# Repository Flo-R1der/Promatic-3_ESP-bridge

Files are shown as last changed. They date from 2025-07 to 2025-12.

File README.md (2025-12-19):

# HÖRMANN Promatic 3 ESPHome Bridge

This project is made to integrate the Hörmann Promatic 3 garage door drive unit into Home Assistant using ESPHome. This approach is more sophisticated compared to other solutions like using an Shelly or similar devices, but comes with some extra functionality:

- ✅ Detects `opening` and `closing` (motor running) as well as `open`/`close` (end position)
- ✅ Does support partially opened states, like `10%` for air ventilation (with auto-stop)
- ✅ can be linked with a Beacon device for zero-touch offline opening
- ✅ is detecting wrong directions and switching the direction if required to gain more specific control, beside the one-touch control
- ✅ highly customizable
- ⚠️ requires PCB assembly and soldering
- ⚠️ requires ESPHome to flash the ESP firmware

> [!CAUTION]  
> Read the [official Manual](TR10A147_E_ProMatic_3_DE.pdf) for safety instruction. Never work on 230V when your're not an expert. Unplug the device before start working for your own safety and to prevent damages while assembling.

| Qty. | Ref.  | Part | Notes |
| :--: | :---: | :--- | :---- |
| 1 | A1 | **MP1584** 3,3V buck regulator | provides 3,3V stabilized; Input: 4,5–28 V |
| 1 | A2 | **ESP8266** D1 Mini or **ESP32** C3 Mini | use ESP32 version for BLE Support |
| 4 | U1-U4 | **PC819** optocoupler | for 24V/3,3V separation |
| 2 | R1-R2 | **2,2kΩ ½W** resistor | series resistor optocoupler LED at 24V |
| 2 | R3-R4 | **330Ω ¼W** resistor | series resistor optocoupler LED at 3,3V |
| 2 | C1-C2 | **0,47μF 35V** capacitor | catch voltage peaks from the driving motor |
| 1 | B1 | **reed switch** | to retrieve the "open" position |
| 1 | S1 | **momentary switch** | optional; for manual open/close/stop trigger |
| 1 | J1 | 2 leg **screw terminal** |  |
| 1 | J2 | 4 leg **screw terminal** |  |
| 1 | J3 | 3 leg **screw terminal** |  |

 A housing is also recommended since the PCB does not fit in the Promatic 3 housing. As reference: I'm using these [project boxes](https://www.amazon.de/dp/B0BWLW941S).

## Option 1: ESP8266 D1 mini
<details>
<summary>For basic functionalities the ESP8266 is totally suitable</summary>

### Circuit Diagram
ESP8266 circuit diagram

### PCB-Design
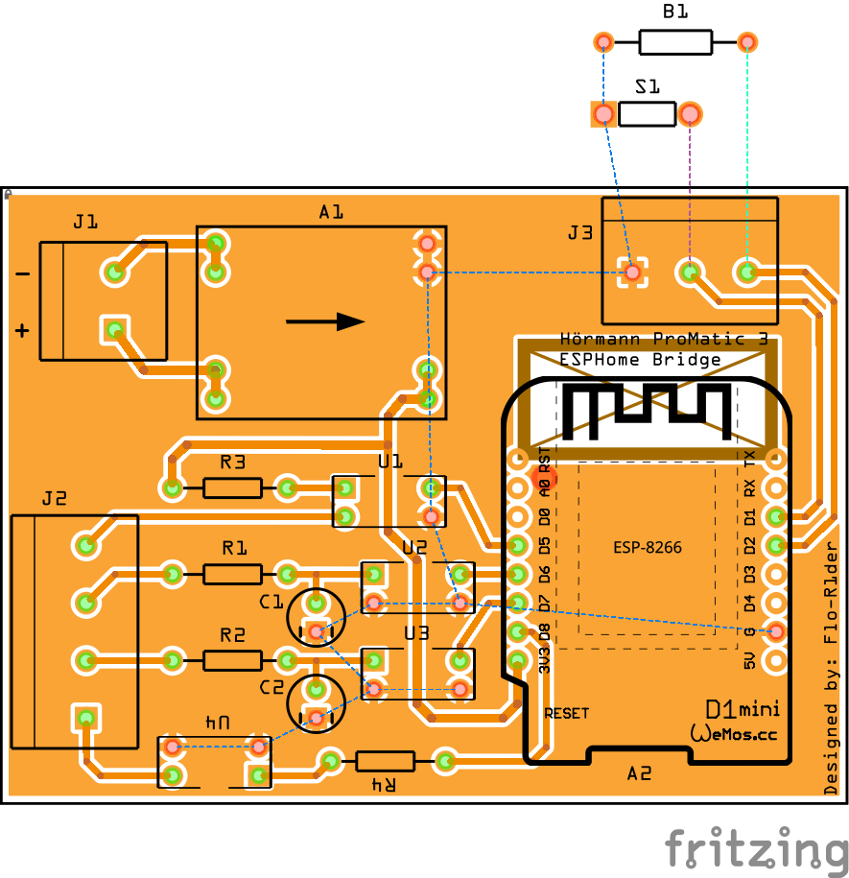
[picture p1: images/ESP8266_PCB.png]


If you like to order the PCB shown above, feel free to use the already exported production files. Or implement changes using **[fritzing](https://fritzing.org/download)** (check the [ESP8266 Pinout Reference](https://randomnerdtutorials.com/esp8266-pinout-reference-gpios/#wemos-d1-mini-pinout)!):
- **PCB-Design**: [ESP8266_extended-gerber.zip](ESP8266_extended-gerber.zip) (76 x 55,7mm)
- **Project File**: [ESP8266.fzz](ESP8266.fzz)

### Results (grid PCB)

I did my prototype on a grip PCB which also works great.  
Grid PCB: 70 x 50 mm / 24 x 18 holes / resistors vertical to save space

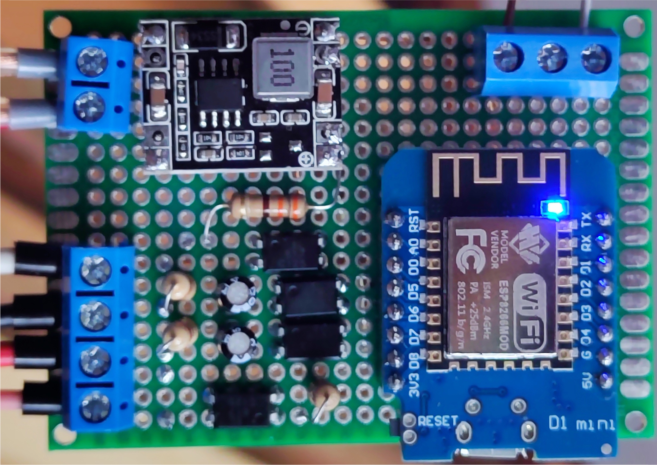
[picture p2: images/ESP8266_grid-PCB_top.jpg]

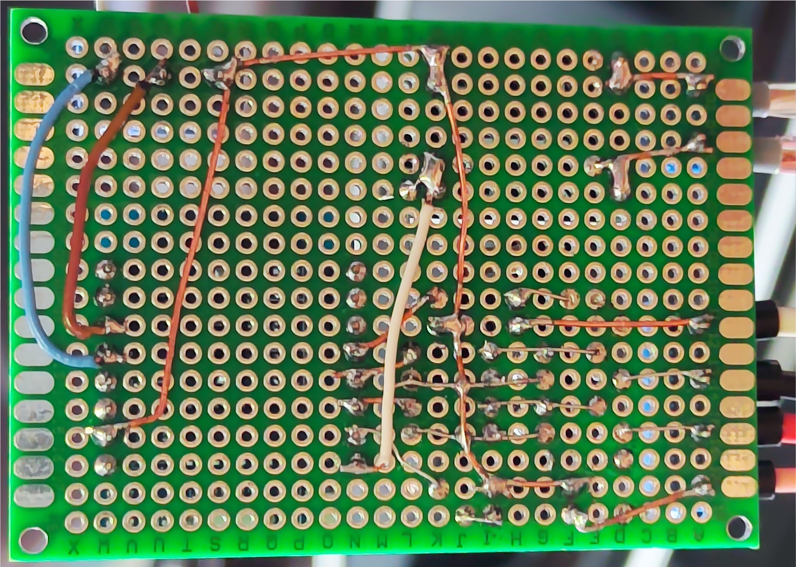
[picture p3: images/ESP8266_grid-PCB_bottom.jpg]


</details>

## Option 2: ESP32 C3 mini
<details>
<summary>For extended functionalities the ESP32 is the better option</summary>

### Circuit Diagram
ESP32-C3-mini circuit diagram

### PCB-Design
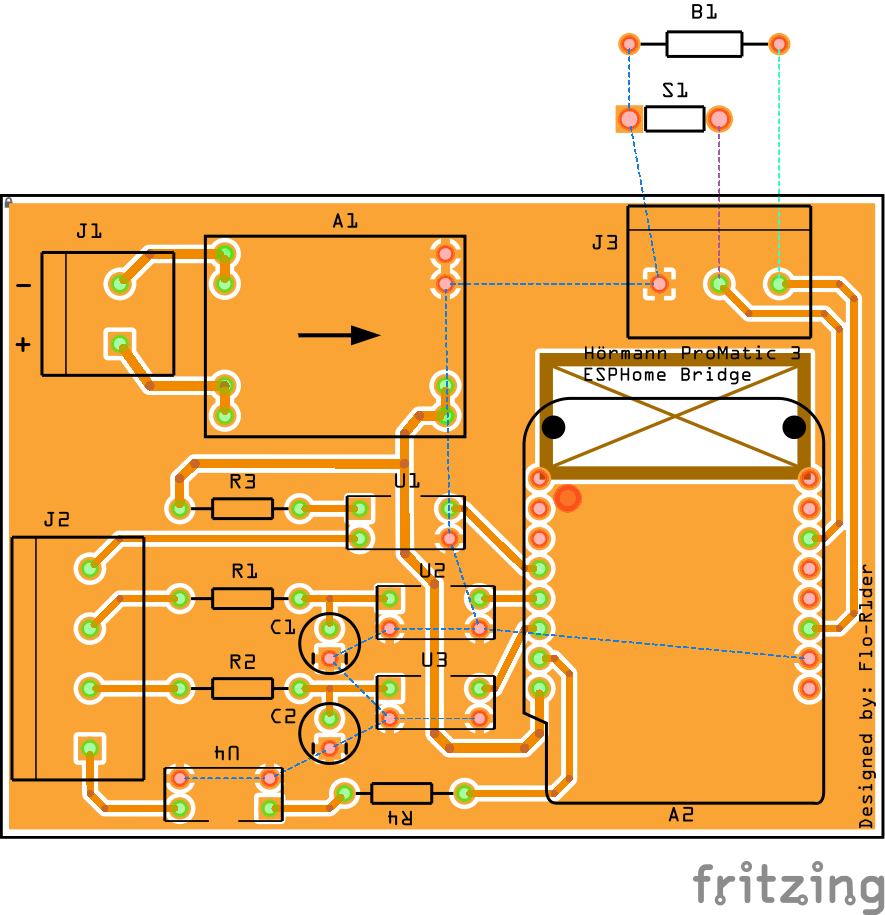
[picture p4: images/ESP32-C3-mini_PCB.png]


If you like to order the PCB shown above, feel free to use the already exported production files. Or implement changes using **[fritzing](https://fritzing.org/download)** (check the [LOLIN ESP32 C3 Mini Pinout Reference](https://www.espboards.dev/esp32/lolin-c3-mini/)!):
- **PCB-Design**: [ESP32-C3-mini_extended-gerber.zip](ESP32-C3-mini_extended-gerber.zip) (78,7 x 54,6mm)
- **Project File**: [ESP32-C3-mini.fzz](ESP32-C3-mini.fzz)

> I tested the ESP32 D1 Mini first, but it was causing a lot of trouble. Therefore, it is now **marked as legacy**. If you still want to use it take, look into the [legacy-folder](legacy/).

### Results (Prototype)

> For the ESP32-D1 mini ([legacy](legacy/)) I ordered a PCB and tried to do the soldering. Unfortunately there were some issues, that are resolved now in all PCB files (see commit [4a13bd1](../../commit/4a13bd1397be6c67168064e2b9723a02679394e2) and [b1b8725](../../commit/b1b872543b13843ac204b23dd64338c8f80fe5ec) for details)

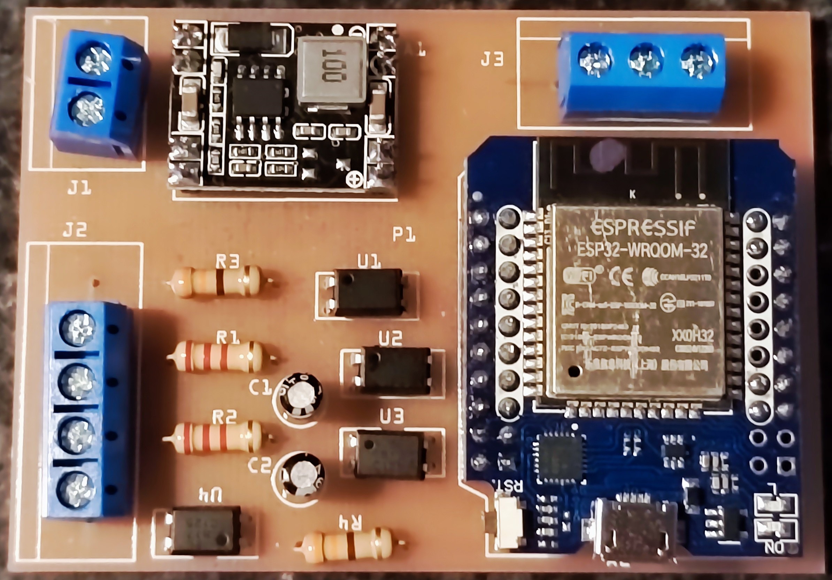
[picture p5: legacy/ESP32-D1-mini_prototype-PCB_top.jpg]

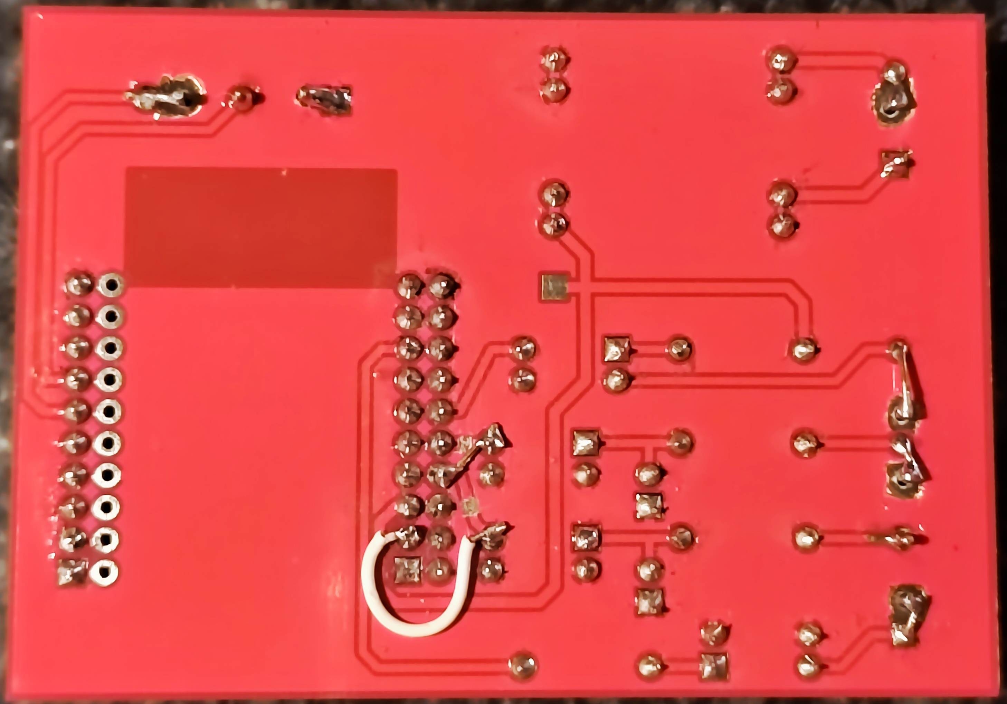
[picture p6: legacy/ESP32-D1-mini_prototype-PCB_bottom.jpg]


</details>

## Connection

> [!WARNING]  
> Unplug the Hörmann drive unit before start working for your own safety and to prevent damages while assembling.

| this PCB | Promatic 3 / Auxiliary | Function | Notes |
| :---: | :--- | :--- | :---- |
| J1.1 | Terminal: 20 | **GND**  | see manual page 25, image 11 |
| J1.2 | Terminal: 5 | **24V**  | see manual page 25, image 11 |
| J2.1 | Terminal: 0V | **closed** state | see manual page 27, image 17 + 20.1 * |
| J2.2 | black motor wire | motor **opening** | pulled to GND when motor is running |
| J2.3 | red motor wire | motor **closing** | pulled to GND when motor is running |
| J2.4 | Terminal: 21 | **open/close/stop** trigger | see manual page 25, image 11 |
| J3.1 | _Auxiliary_: reed switch <br> _Auxiliary_: momentary switch | common **GND** | may have two wires |
| J3.2 | _Auxiliary_: momentary switch | **manual trigger** | optional; pulled to GND as a trigger |
| J3.3 | _Auxiliary_: reed switch | **open** state | pulled to GND when triggered |

To find the correct Terminal on this project's PCB please use the circuit diagrams and the official handbook as reference:
- [ESP8266_circuit-diagram.pdf](ESP8266_circuit-diagram.pdf)
- [ESP32-C3-mini_circuit-diagram.pdf](ESP32-C3-mini_circuit-diagram.pdf)
- [TR10A147_E_ProMatic_3_DE.pdf](TR10A147_E_ProMatic_3_DE.pdf) (or see pictures below)

| Image 11 | Image 17 * | Image 20.1 * |
| :---: | :---: | :---: |
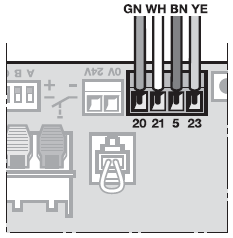
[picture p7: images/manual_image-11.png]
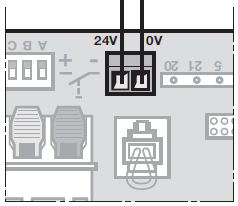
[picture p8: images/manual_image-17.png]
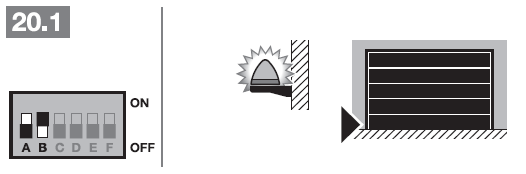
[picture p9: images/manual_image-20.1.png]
|  |  |  |

\* As can be seen in Image 20.1, the **DIP switch B** must be turned **ON**. This is required, so that the Terminal 0V (Image 17) gets activated when the Promatic 3 detects the garage door as closed. This will then subsequential set the garage door state in the ESP and Home Assistant to `closed`.

Once everything is connected, do a short test, put the project box on top of the drive unit and close the cover:

<table>
  <tr>
    <td rowspan="2" width=50%>Connection:<br>
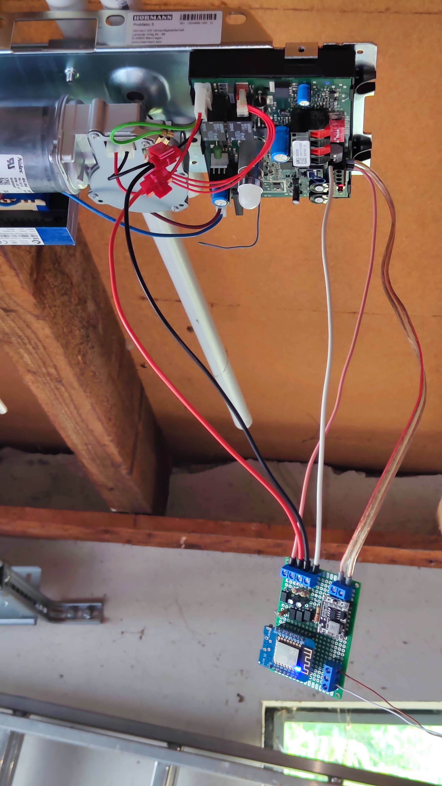
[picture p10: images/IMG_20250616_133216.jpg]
      </td>
    <td>Box placement:<br>
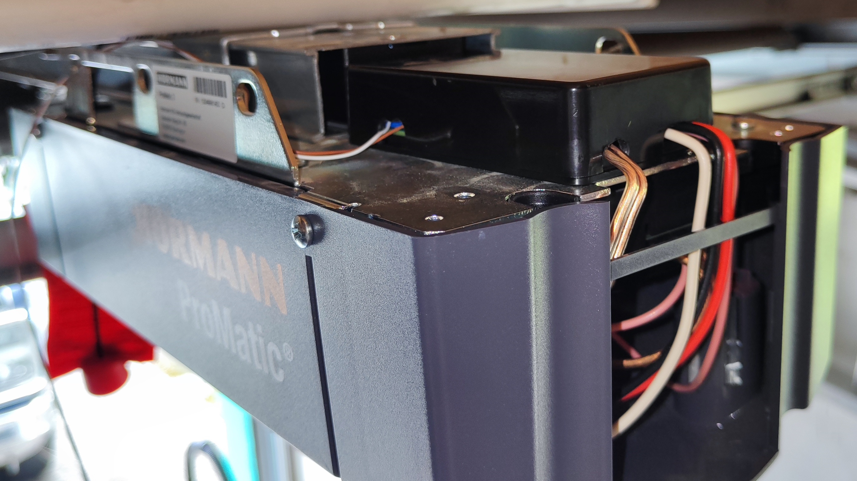
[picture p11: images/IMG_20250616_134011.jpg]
      <br>
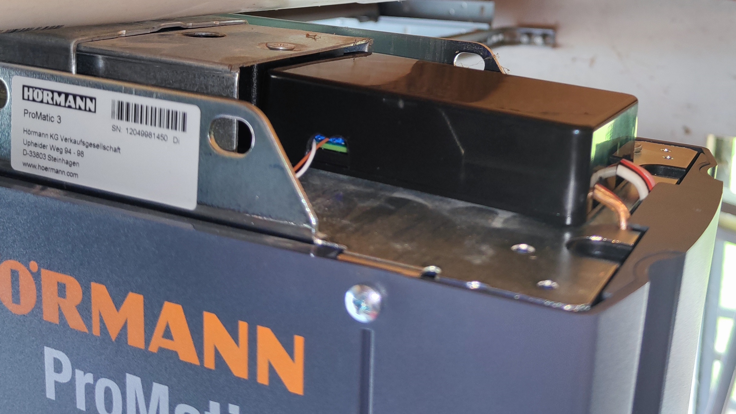
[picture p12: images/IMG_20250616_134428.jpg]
      </td>
  </tr>
  <tr>
    <td>Open sensor (reed contact J3.1+J3.3):<br>
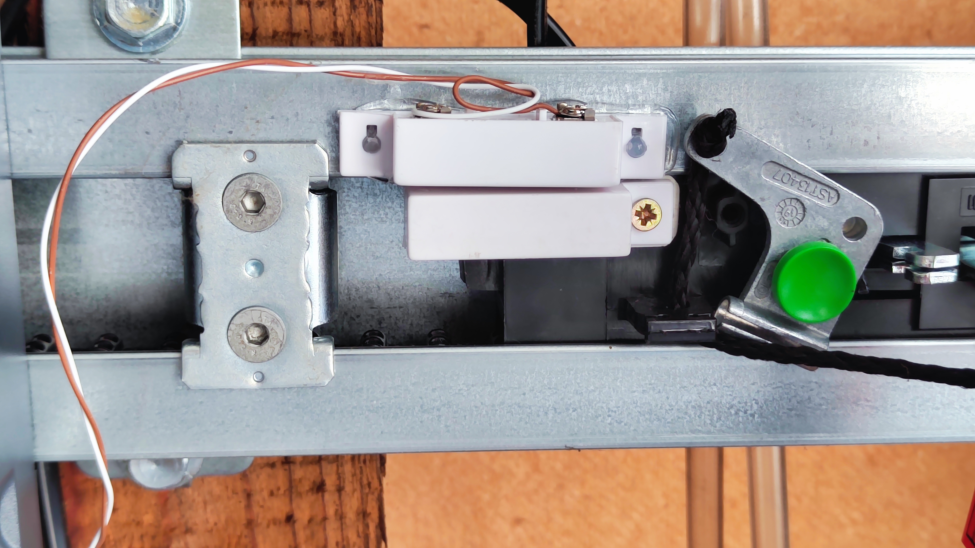
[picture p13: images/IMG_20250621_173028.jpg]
      </td>
  </tr>
</table>

## ESPHome Firmware

### ESP8266 D1 mini
> **Firmware Template: [ESP8266.yaml](ESP8266.yaml)**

This file contains the basic configuration. You may change the values in the first 17 lines according to your favor. Changes beyond line 17 can break the functionality. If you want to add additional functionalities, feel free to add your yaml-code at the end. The default code exposes the following entities to Home Assistant:
- **Cover-Entity**
  - with percentage % control (`device_class: garage`)
- **Binary Sensors**
  - From every GPIO; deactivated by default (open, closed, opening, closing, external button press, manual trigger)
- **Diagnostics** (Connection Status, WiFi Signal)

### ESP32 C3 mini
> **Firmware Template: [ESP32-C3-mini.yaml](ESP32-C3-mini.yaml)**

> [!NOTE]
> The board I used is the [LOLIN ESP32 C3 Mini](https://www.espboards.dev/esp32/lolin-c3-mini/) which has a RGB onboard LED. These RGB-LEDs are not supported by the [ESPHome Status-LED](https://esphome.io/components/light/status_led/). So I wrote a quick package, utilizing the onboard RGB LED to display the status of the board. Details can be found in my [ESPHome RGB Status LED Package](https://github.com/Flo-R1der/ESPHome_RGB-Status-LED_Package).

This file is basically a copy of the ESP8266 and is working the same way. Also the entities mentioned above are similar. However, the ESP32 has some considerable extras defined:
- **Bluetooth Beacon**
  - can be used to identify the vehicle or occupancy of the garage.
  - To discover bluetooth beacons, you might use the [discovery code](ESP32-C3-mini_beacon-discovery.yaml) first.
- **Bluetooth Proxy**
  - To proxy bluetooth signals (button press, BLE-sensors, etc.) to your Home Assistant instance.

> I tested the ESP32 D1 Mini first, but it was causing a lot of trouble. Therefore, it is now **marked as legacy**. If you still want to use it take, look into the [legacy-folder](legacy/).

<br>

---

## Home Assistant Automation

> [!NOTE]  
> This repository aims to provide the ESP device and its directly related elements (circuit diagram, PCB, ESPHome-yaml, ...). Therefore, this section here is only for information, but without further support.

**Prerequisite**:   
Make sure, the **Background Location** is enabled on your phone and [set up correct](images\background-location.jpg).

<br>

Here are the two automation I'm using in combination with the ESP8266 and ESP32:
- **Trigger** is always the distance to the Garage/Home-Zone from the [**Proximity Sensors**](https://www.home-assistant.io/integrations/proximity/):
   - below: 20 = ARRIVING | above: 100 = LEAVING
- **Condition** is important to filter, weather you are in your car and not, using taxi/bus/bicycle/feet:
   - _Variant 1_: Enable the [**Android Auto Sensor**](https://companion.home-assistant.io/docs/core/sensors/#android-auto) and check if connected or not.
   - _Variant 2_: Utilize the [**Bluetooth Sensors**](https://companion.home-assistant.io/docs/core/sensors/#bluetooth-sensors) to look for a specific connected Bluetooth Device.
   - _BLE Option_: With the [ESP32 **Bluetooth Low Energy Tracker**](https://esphome.io/components/esp32_ble_tracker/) you can detect, if the garage is already occupied.
- **Action** simply open or closes the garage:
   - if ARRIVING and garage closed: `cover.open_cover`
   - if LEAVING and garage opened: `cover.close_cover`

Here's the YAML-Code for my two examples:
- [Automation 1](automation_1.yaml): using Condition _Variant 1_
- [Automation 2](automation_2.yaml): using Condition _Variant 2_ and the _BLE Option_

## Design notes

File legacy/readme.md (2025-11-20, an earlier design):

> [!IMPORTANT]  
> The ESP32 D1 Mini was causing a lot of trouble. Therefore it is now **marked as legacy**. If you still want to use it and experience the same, here is what I did to overcome the issues:
> 1. The ESP32 D1 mini does not have a BOOT button. To put the device in FLASH-Mode, **`GPIO0` must be connected to `GND`** ([Pinout Reference](https://www.espboards.dev/esp32/d1-mini32/)).
> 2. The [ESPHome Web Installer](https://web.esphome.io/) wasn't connecting to my device, but **the [Tasmota Web Installer](https://tasmota.github.io/install/) worked _sometimes_.**
> 3. To ensure proper connection I installed [ESPHome on the local PC](https://esphome.io/guides/installing_esphome/). From there I was able to **[compile and flash](https://esphome.io/guides/getting_started_command_line/#first-uploading) from the shell**.  
>    - Command: `esphome run garage.yaml` _(you may adapt the yaml-name)_
> 4. When something seems to be corrupt an `erase-flash`-command from the [Espressif ESPTool](https://docs.espressif.com/projects/esptool/en/latest/esp32/) may help performing a **factory reset, if required** (see also [this Tutorial](https://randomnerdtutorials.com/esp32-erase-flash-memory/)).
> 5. The more modern **framework type `esp-idf` was causing boot-loops** on the ESP32 D1 mini, whenever **WiFi is enabled**.
> 6. Switching to  `arduino` framework was causing an **oversized firmware, with bluetooth components** enabled. Therefore, I disabled the fallback-hotspot and captive portal to reduce it's size, which removes the ability to update WiFi-password from the device hotspot.
> 7. When powering the ESP32 D1 Mini **with 3.3V only, the device would not start** most of the times. With additional USB power connected it's starting, but that is just a workaround. At least when started and USB disconnected, the device was capable to do everything as expected, including OTA-Updates.

### ESP32 D1 mini

> **Firmware Template: [ESP32-D1-mini.yaml](ESP32-D1-mini.yaml)**

This file is basically a copy of the ESP8266 and is working the same way. Also the entities mentioned above are similar. However, the ESP32 has some considerable extras defined:
- **Bluetooth Beacon**
  - can be used to identify the vehicle, on which the garage door should open.
  - To discover bluetooth beacons, you might use the [discovery code](ESP32_beacon-discovery.yaml) first.
- **Bluetooth Proxy**
  - To proxy bluetooth signals (button press, BLE-sensors, etc.) to your Home Assistant instance.

<br>

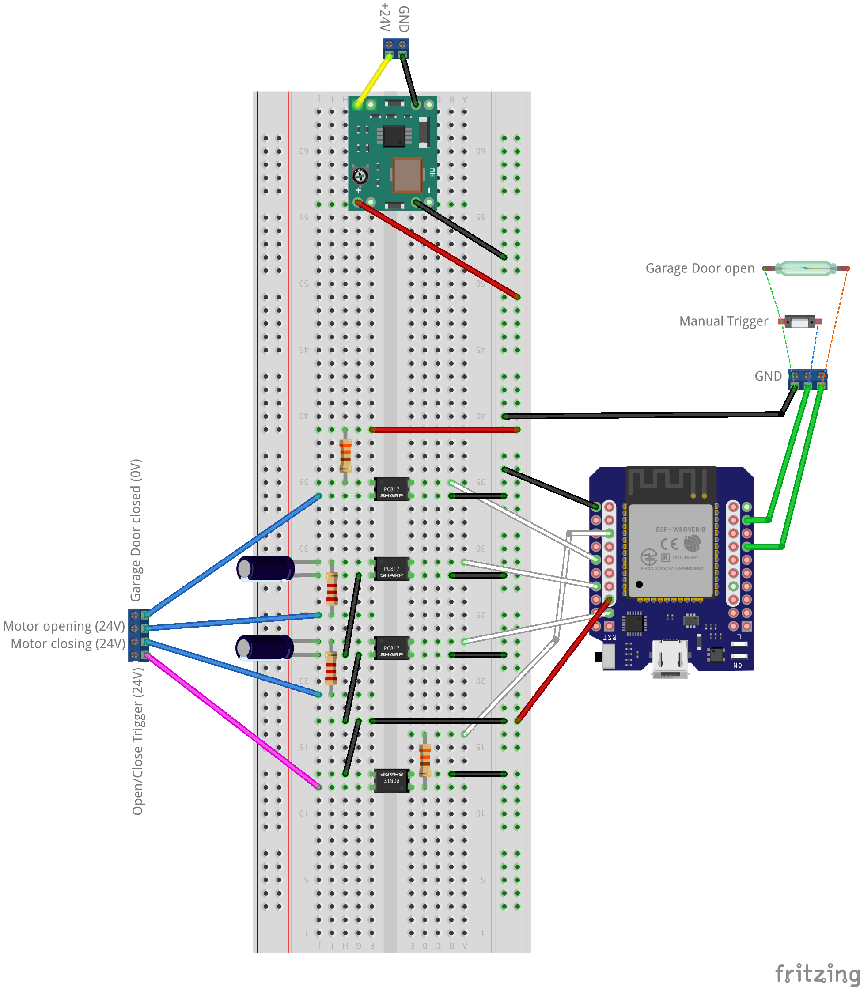
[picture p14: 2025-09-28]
images/ESP32-D1-mini_Breadboard.png

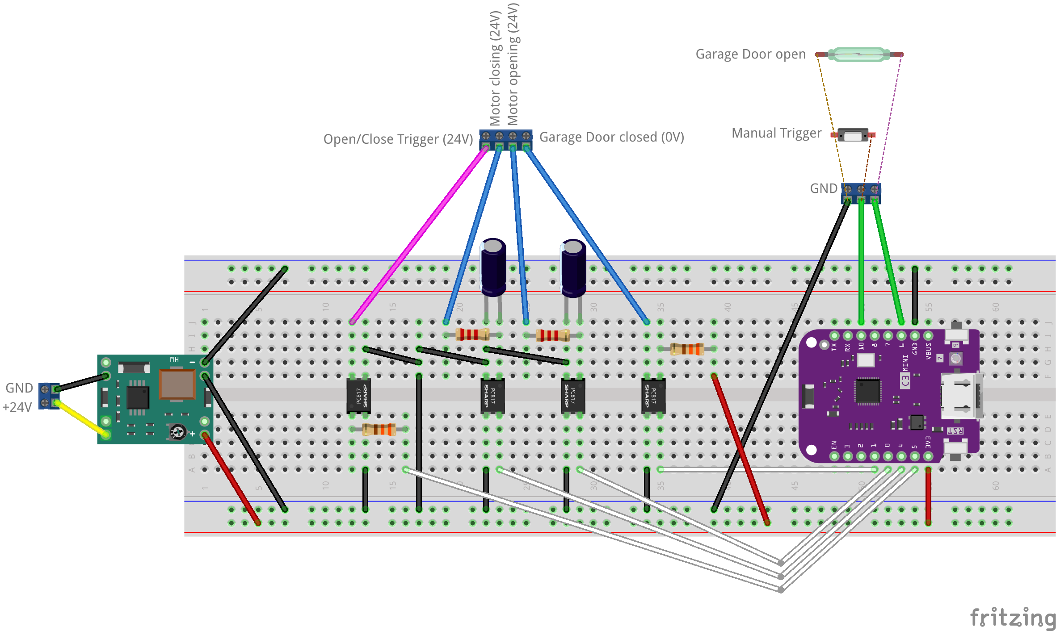
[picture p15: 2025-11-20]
images/ESP32-C3-mini_Breadboard.png

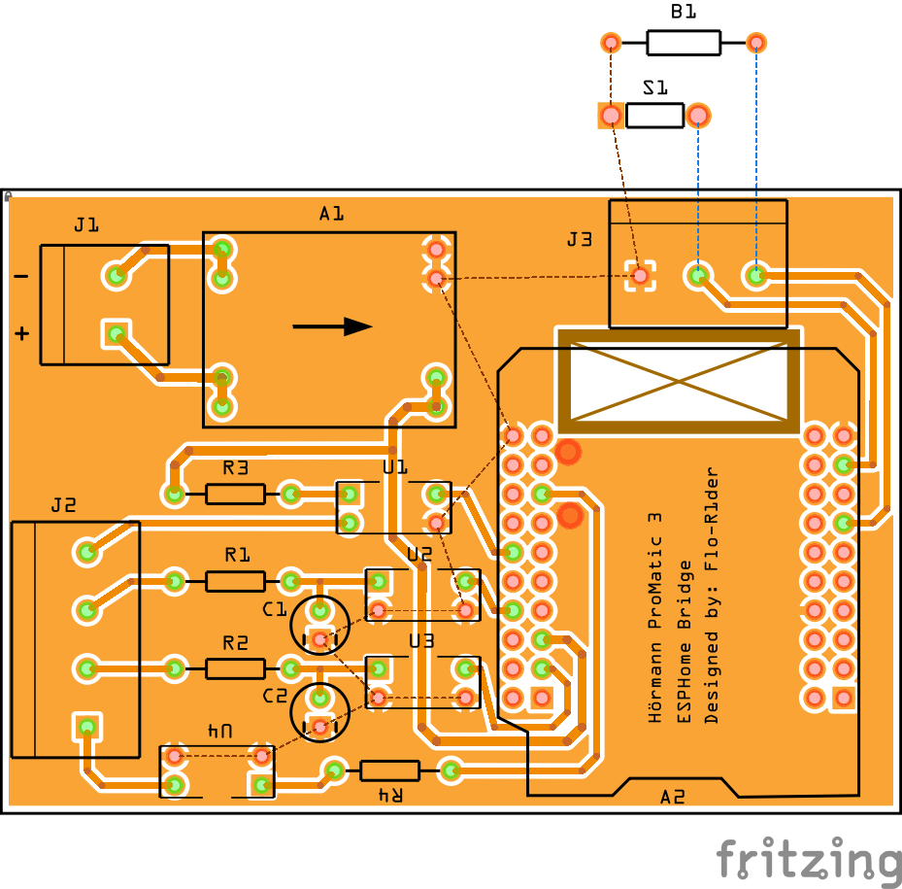
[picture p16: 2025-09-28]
images/ESP32-D1-mini_PCB.png

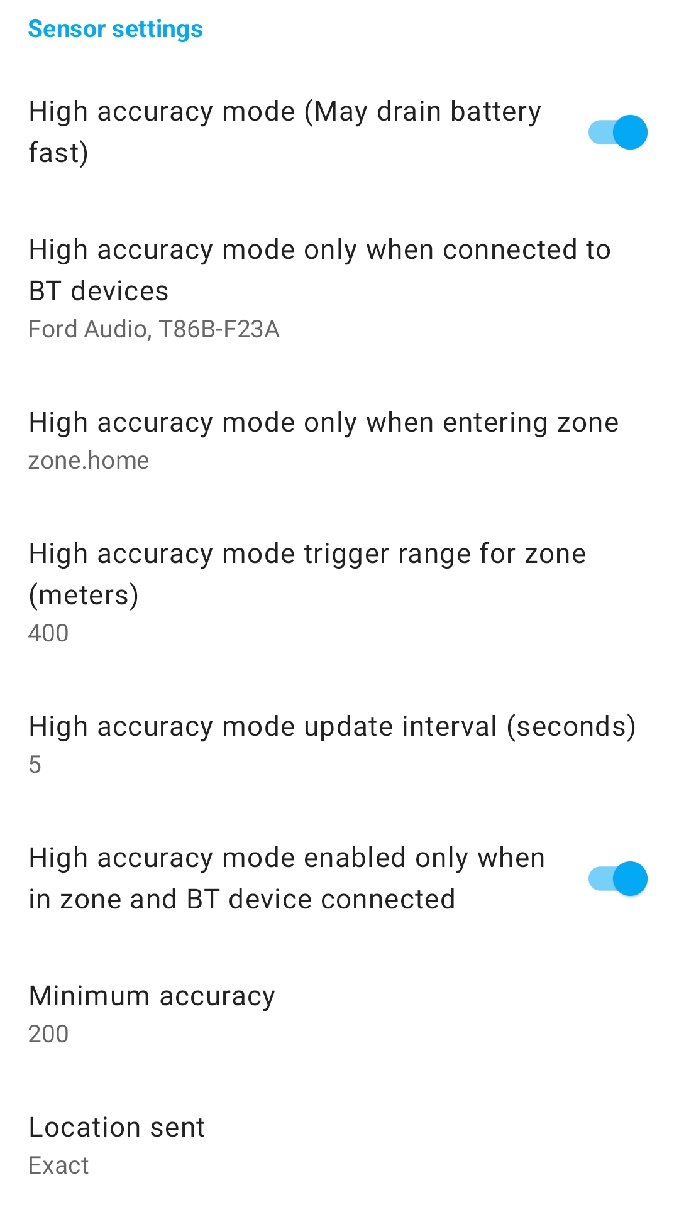
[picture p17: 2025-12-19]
images/background-location.jpg

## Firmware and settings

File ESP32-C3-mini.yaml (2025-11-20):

#===== You can edit your configuration in this 'substitution' section =====#
substitutions:
  device_name: "garage-rechts"  # only lowercase, numbers, - and _ allowed!
  friendly_name: "Garage rechts"
  wifi_ssid: !secret wifi_ssid
  wifi_password: !secret wifi_password
  local_domain: ".fritz.box"
  hotspot_password: !secret hotspot_password
  ota_password: !secret ota_password
  api_encryption_key: !secret api_encryption

  # Set the open and close durations of your garage door here (decimal seconds allowed)
  # Measure the time your garage door needs for a full open/close cycle
  open_duration: 13.8s
  close_duration: 14.8s

  # BLE Beacon settings
  ble_beacon_mac: !secret ble_beacon_mac_1
  ble_timeout: 60s

light:
  - platform: esp32_rmt_led_strip
    id: system_status_led             # DO NOT CHANGE
    pin: GPIO7                        # check your board
    rgb_order: GRB                    # check your board
    num_leds: 1
    chipset: ws2812                   # check your board
    name: "onboard LED"
    disabled_by_default: true
    default_transition_length: 200ms
    icon: mdi:led-outline
    restore_mode: ALWAYS_OFF
    effects:
      - pulse:
          name: "Slow Pulse"          # REQUIRED
          update_interval: 2s         # can be adjusted
      - pulse:
          name: "Fast Pulse"          # REQUIRED
          update_interval: 500ms      # can be adjusted

packages:
  rgb_status_led: 
    url: https://github.com/Flo-R1der/ESPHome_RGB-Status-LED_Package
    file: status_led_package.yaml

##### Changes beyond this line may break the functionality #####

esphome:
  name: ${device_name}
  friendly_name: ${friendly_name}

esp32:
  board: lolin_c3_mini
  framework:
    type: esp-idf

logger:
  baud_rate: 0

api:
  encryption:
    key: ${api_encryption_key}

ota:
  - platform: esphome
    password: ${ota_password}

wifi:
  ssid: ${wifi_ssid}
  password: ${wifi_password}

  domain: ${local_domain}
  use_address: 192.168.178.180
  
  ap:
    ssid: ${device_name}
    password: ${hotspot_password}

  output_power: 14dB   # higher power was causing instability on the ESP32-C3-mini


captive_portal:
  

esp32_ble_tracker:


sensor:
  - platform: wifi_signal # Reports the WiFi signal strength/RSSI in dB
    name: "WiFi Signal dB"
    id: wifi_signal_db
    update_interval: 60s
    entity_category: "diagnostic"
    icon: mdi:wifi

  - platform: copy # Reports the WiFi signal strength in %
    source_id: wifi_signal_db
    name: "WiFi Signal %"
    filters:
      - lambda: return min(max(2 * (x + 100.0), 0.0), 100.0);
    unit_of_measurement: "%"
    entity_category: "diagnostic"
    device_class: ""
    icon: mdi:wifi


  - platform: ble_rssi
    mac_address: ${ble_beacon_mac}
    name: "BLE-Beacon RSSI"
    id: ble_beacon_rssi
    disabled_by_default: true
    filters:
      - throttle: 30s   # throttle state publish to home assistant / prevent updates in 300ms intervals 


output:
  - platform: gpio
    pin: 
      number: GPIO5
    id: gpio_impulse


button:
  - platform: output
    id: open_close_impulse
    output: gpio_impulse
    duration: 300ms


binary_sensor:
  - platform: status
    name: "Status"

  - platform: gpio
    pin:
      number: GPIO10
      mode:
        input: true
        pullup: true
      inverted: true
    name: "Button"
    id: external_button
    disabled_by_default: true
    filters:
      - delayed_on: 50ms
      - delayed_off: 50ms
    on_press:
      then:
        - button.press: open_close_impulse

  - platform: gpio
    pin:
      number: GPIO6
      mode:
        input: true
        pullup: true
      inverted: true
    id: is_opened
    name: "open"
    disabled_by_default: true
    filters:
      - delayed_on: 50ms
      - delayed_off: 50ms

  - platform: gpio
    pin:
      number: GPIO1
      mode:
        input: true
        pullup: true
      inverted: true
    id: is_closed
    name: "closed"
    disabled_by_default: true
    filters:
      - delayed_on: 50ms
      - delayed_off: 50ms

  - platform: gpio
    pin:
      number: GPIO0
      mode:
        input: true
        pullup: true
    id: motor_opening
    name: "opening"
    disabled_by_default: true
    filters:
      - delayed_on: 50ms
      - delayed_off: 50ms
      # the voltage of the motor drops at the end to slow down the garage door
      # which turns off the motor_opening detection and puts the cover in a 
      # false idle state. The delayed_off: 3300ms time can compensate this behavior, 
      # but a partial "open" state will return wrong % values.
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

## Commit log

2025-06-24 ESP8266 circut planning
    [ESP8266.fzz]
2025-07-20 update circuit diagram, add images and extended gerber for ESP8266
    [ESP8266.fzz]
2025-07-21 ESP32 circuit planning
    [ESP32-mini.fzz]
2025-07-21 ESP32-mini and general documentation
2025-08-01 fixed pcb failures
    [ESP32-mini.fzz, ESP8266.fzz]
2025-09-05 ESP32 mini Prototype documentation
2025-09-05 ESP32 mini PCB-changes from Prototype
    [ESP32-mini.fzz]
2025-09-05 ESP32 mini first YAML upload
2025-09-28 ESP32 D1 mini pin update > resolve strapping pins warning
    [ESP32-mini.fzz]
2025-10-03 ESP32 files renamed
    [ESP32-D1-mini.fzz]
2025-10-03 implement ESP32 BLE-Beacon Present logic
2025-10-03 auto-detect wrong direction and switch to correct direction
    [ESP32-D1-mini.yaml]
2025-10-05 ESP logging and auto-detect for wrong direction improved
    [ESP32-D1-mini.yaml]
2025-11-20 marked ESP32-D1-mini as legacy
    [ESP32-D1-mini.fzz]
2025-11-20 introduce the ESP32-C3-mini
    [ESP32-C3-mini.fzz]
2025-11-20 update readme to ESP32 D1 Mini
